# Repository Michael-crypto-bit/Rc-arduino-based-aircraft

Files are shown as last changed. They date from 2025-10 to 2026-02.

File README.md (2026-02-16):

a repository of all files needed to recreate my aircraft, only use the most updated ones as some originals were dicarded, and are only here to show the path I took
items needed:
2 ESCs 30-40a with 2200kv motors                                                                                                                                                    
arduino Nano
2 micro servos
xt-60 cable y splitter male to dual female output                                                                                                                                                                
plastic glue                                                                                                 
duct tape                                                                                                                                                                                            
foam                                                                                                      
fpv camera optional                                                                                                                                                                                           
fishing wire optional                                                                                                                   
wooden dowels                                                                                                                                                        
lipo battery - must match the draw of motors, they will power arduino in turn                                                                                                   
lw pla and 3d printer                                                                                                                                                                               
a lasercutter with lightweight wood medium basswood hardwood or balsa
assembly steps: 
1) 3d print wings with lw pla and attach to each other with wooden dowels, the dowels will slot into the small circular holes in the side of each wing segment
2) screw in 2200kv motors and connect ESC's sliding the ESC into the larger hole in the wing, once for each wing
3) put in servos into the smaller hole with the arm base facing towards the trailing edge of the wing, with cable exstensions going in the direction of the 2200 kv motors and eventually towards the body. All cables will run through the holes in the wing


5) after all electronics are placed and dowels have been slotted into the wings enclose with duck tape to bind the wings together and enclose electronics
6) assemble the body sections with glue, attach rear wings with two more dowels or thick wire and glue in place
7) carve a the rear tail out of foam and attach with dowels and glue

8) slot the wings onto the front of the body and route wires through the roof of the electronics compartment, attach optional camera through the front mounting hole
9) if the wings are too heavy for the dowels, and they start to bend use fishing wire and wooden support on the roof in a tent style to raise the wings, or use dowels underneath the wing
    
11) insert the bread board, arduino nano, and switch into the electronics compartment, making sure the switch is secure and electronically sound
    
12) when ready to fly program the arduino and plug in the lipo battery into a cable splitter connecting the two ESC's and the plane will start on its own
                                                                                                          
link to documentation: https://docs.google.com/document/d/1xMwoFOoDOEly96luMzOv4UvHKFmw87LAqAQyq4E37es/edit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                                                              
-------------------------------------------------------UPDATE 1/5/2026--------------------------------------------------
I have designed an all in one pcb board for the arduino pro mini and extras including a reciever, gyro and more all in one board. I am moving to the arduino pro mini mainly for it's size while still having the same arduino base which is the purpose of this project. These are being shipped from pcbway.com and the review will be uploaded shortly.
    This update will allow the aircraft to be fully rc, arduino code is soon to follow.
-------------------------------------------------------UPDATE 2/4/2026--------------------------------------------------
The long awaited pcb boards have arrived from PCBway.com. At a firts glance they look quite professional in their black, their is no issues or malformations in their design. I am very happy with the quality. Pictures are soon to follow. My complete review will be updated when I have completely sautered and tested the pcb boards.
-------------------------------------------------------UPDATE 2/16/2026---------------------------------------------------                                                                                           
Assembly has started for the PCB boards, and v1 of the gerbers will be uploaded to this repository, also here are the pictures that were promised, again a great thanks to PCBway.com for generously supplying these high quality PCB boards. The files for the transmitter can be found on https://howtomechatronics.com/projects/diy-arduino-rc-transmitter/







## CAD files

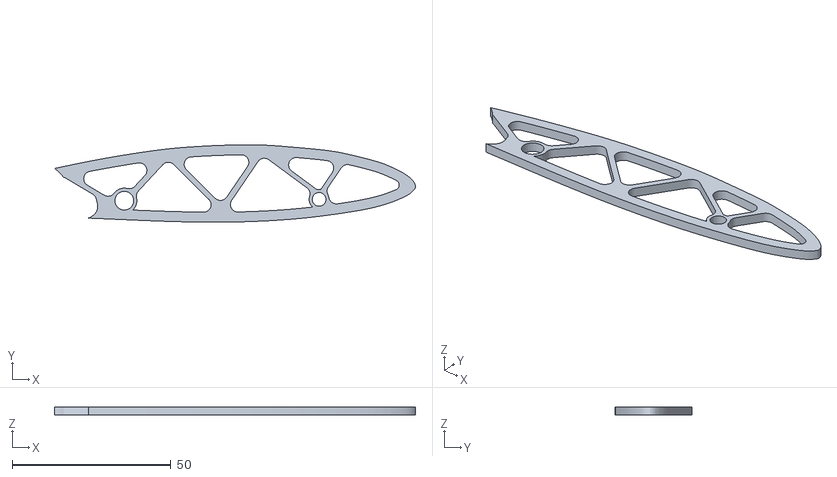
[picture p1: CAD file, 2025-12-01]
Airfoil v7 struts.stl
113.8 x 24.4 x 2.54

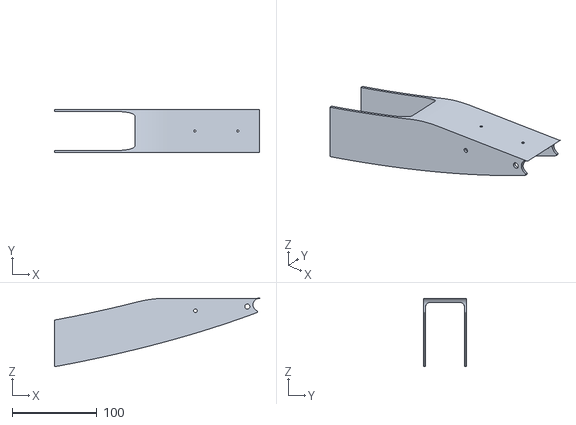
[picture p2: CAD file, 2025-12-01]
plane v1 with 7 inch wings rear.stl
241.5 x 50.8 x 80.7

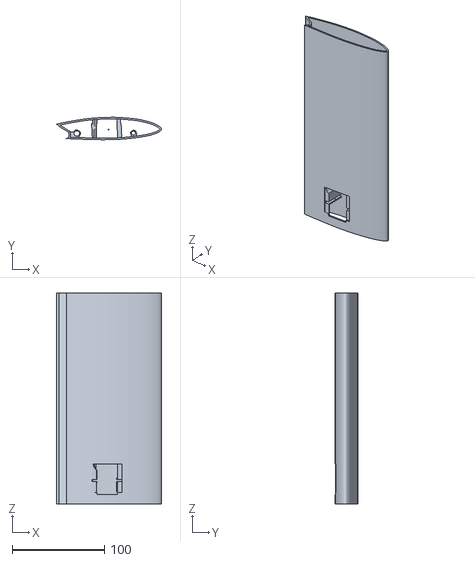
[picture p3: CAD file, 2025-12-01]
Airfoil v7 lightweight single.stl
113.8 x 24.4 x 228.6

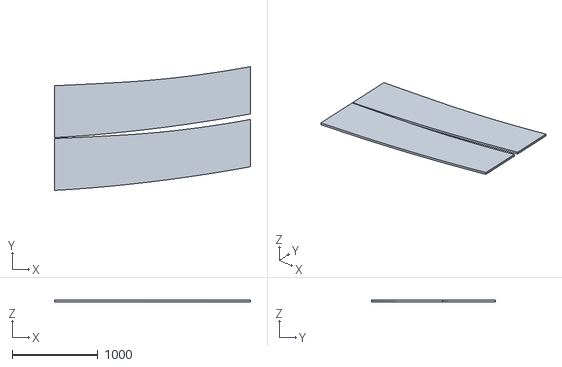
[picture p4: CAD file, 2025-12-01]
plane v2 with 7 inch wings side panel.stl
2280.4 x 1440.6 x 26.0

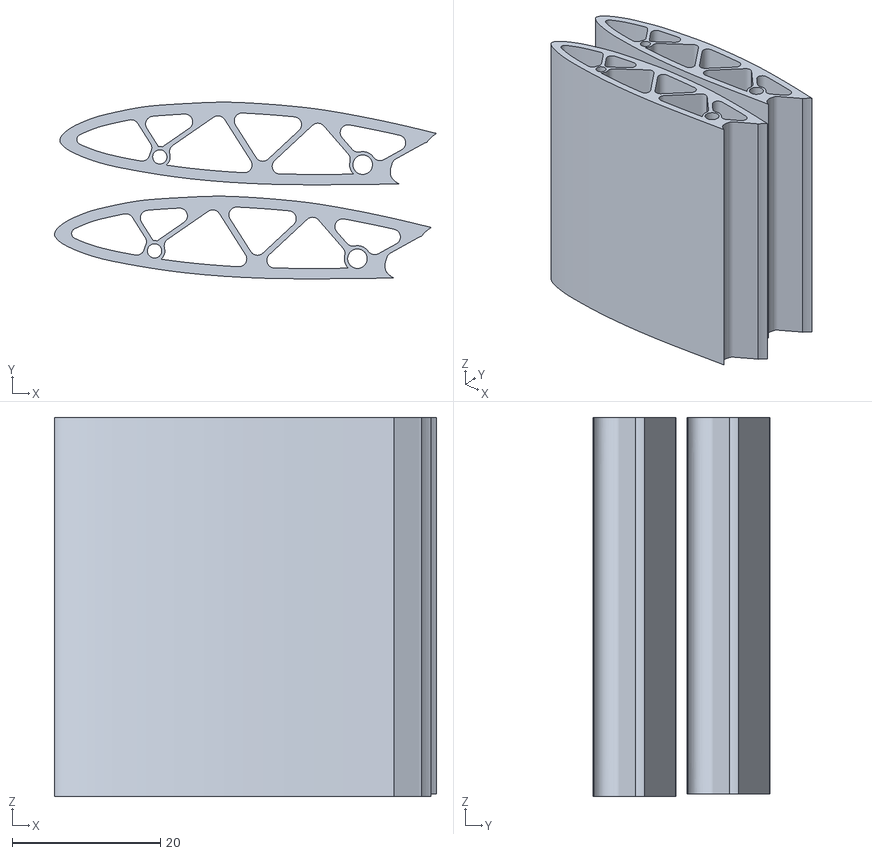
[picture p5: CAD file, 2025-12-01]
rear wings.stl
51.5 x 23.8 x 51.2

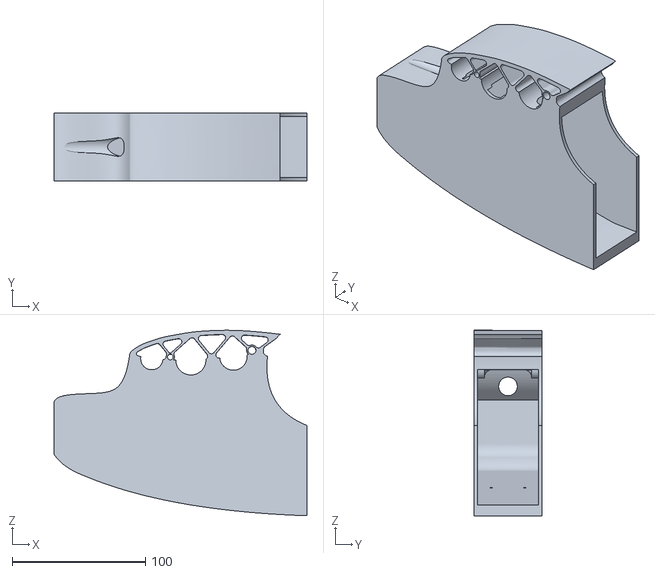
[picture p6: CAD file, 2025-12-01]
v3 front of plane.stl
189.7 x 50.8 x 139.1

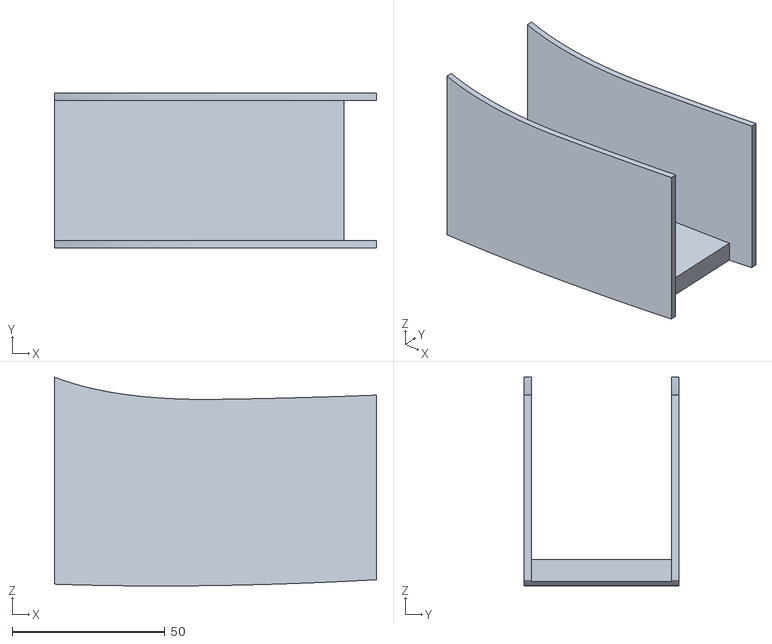
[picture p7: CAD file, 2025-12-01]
front middle section.stl
105.3 x 50.8 x 68.3

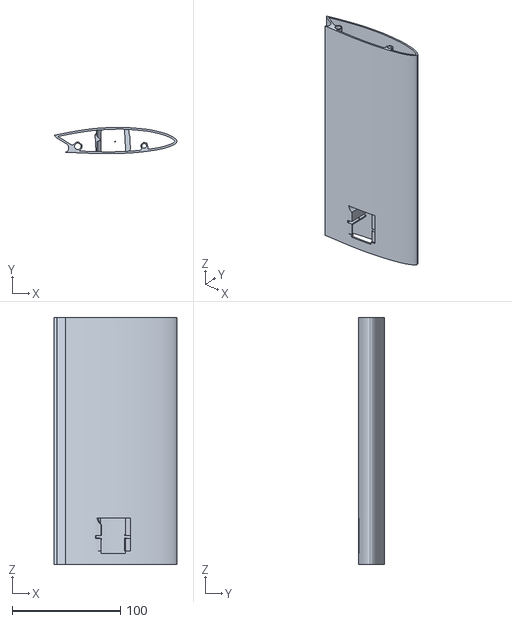
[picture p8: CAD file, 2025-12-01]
Airfoil v6 single lightweight.stl
113.8 x 24.4 x 228.6

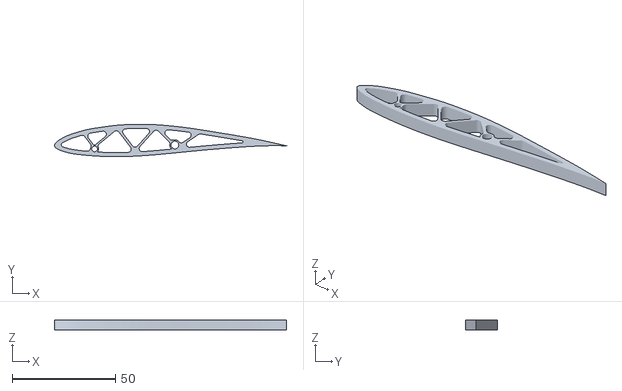
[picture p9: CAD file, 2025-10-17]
Airfoil.stl
112.4 x 15.6 x 5.00

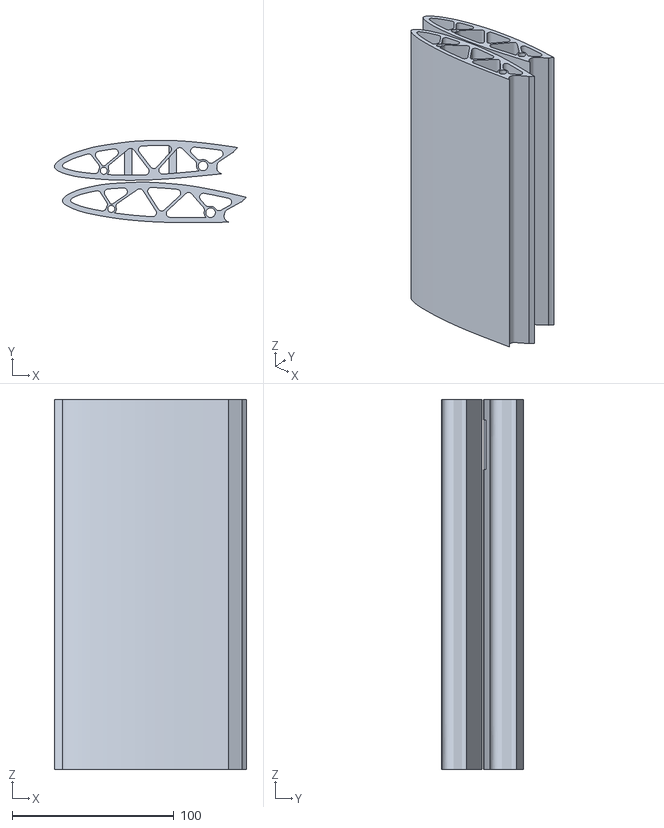
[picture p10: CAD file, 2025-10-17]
Airfoil v5.stl
118.8 x 50.7 x 228.6

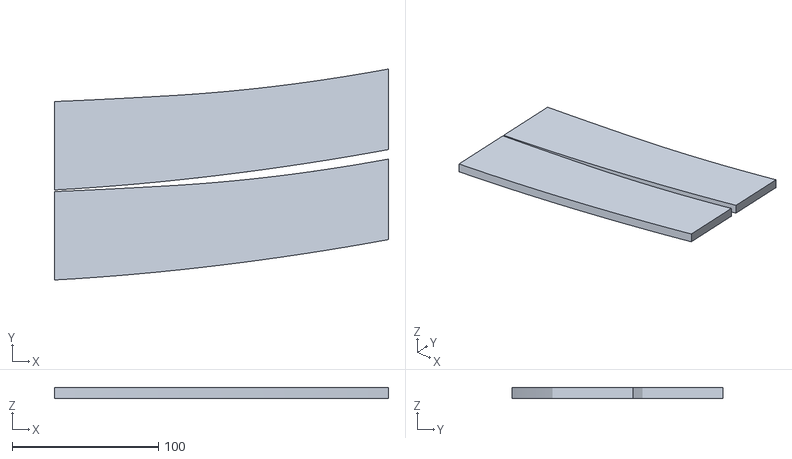
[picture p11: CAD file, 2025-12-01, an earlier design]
plane v1 with 7 inch wings side panel.stl
228.0 x 144.1 x 7.79

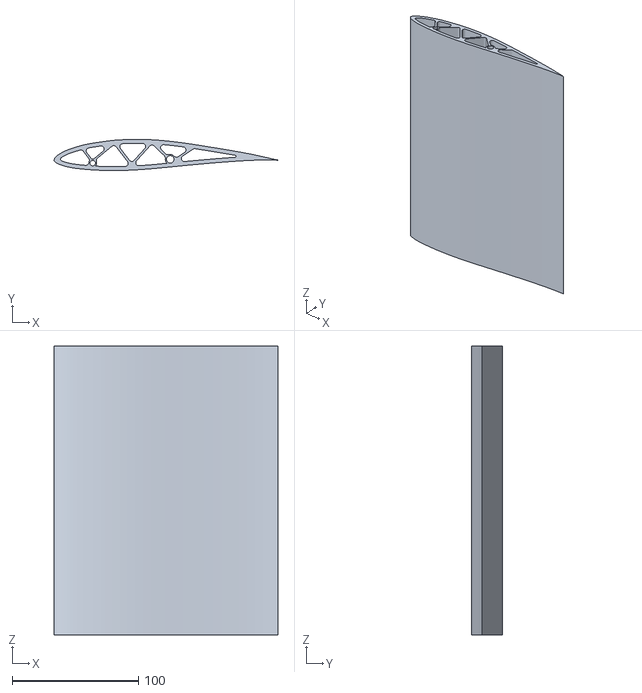
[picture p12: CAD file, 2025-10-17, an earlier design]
Airfoil v3.stl
177.0 x 24.6 x 228.6

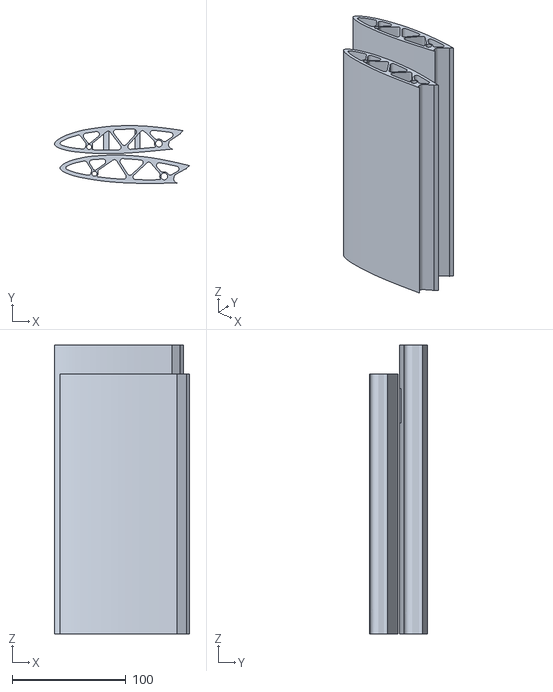
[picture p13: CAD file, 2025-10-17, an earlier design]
Airfoil v4.stl
118.8 x 50.7 x 254.0

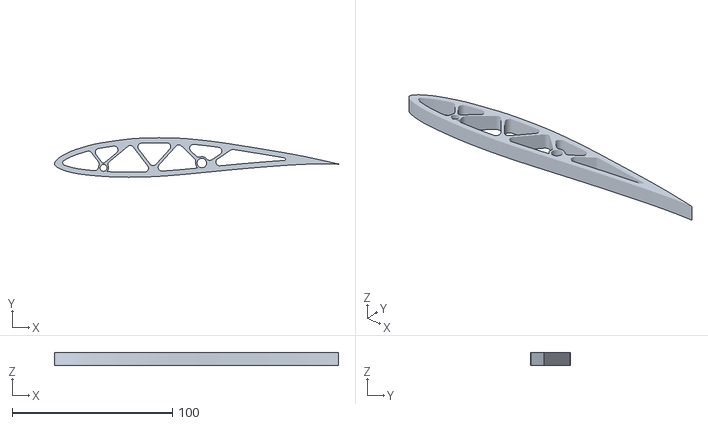
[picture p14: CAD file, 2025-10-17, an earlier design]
Airfoil v1.stl
177.0 x 24.6 x 7.87

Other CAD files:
Airfoil v2.stl

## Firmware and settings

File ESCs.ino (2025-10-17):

#include <Servo.h>
#define CLK 11
#define DT 10

int counter = 20;
int currentStateCLK;
int lastStateCLK;
String currentDir = "";

Servo ESB;
Servo ESC; 

int Speed; 

void setup(){
  Serial.begin(9600);
ESB.attach(12,1000,2000);
ESC.attach(9,1000,2000);
  pinMode(CLK, INPUT);
  pinMode(DT, INPUT);
  lastStateCLK = digitalRead(CLK);
}

void loop(){

  // Read the current state of CLK
  currentStateCLK = digitalRead(CLK);

  // If last and current state of CLK are different, then pulse occurred
  // React to only 1 state change to avoid double count
  if (currentStateCLK != lastStateCLK && currentStateCLK == 1) {

    // If the DT state is different than the CLK state then
    // the encoder is rotating CCW so decrement
    if (digitalRead(DT) != currentStateCLK) {
      counter--;
      currentDir = "CCW";
    } else {
      // Encoder is rotating CW so increment
      counter++;
      currentDir = "CW";
    }

    Serial.print(" | Counter: ");
    Serial.println(counter);
  }

  // Remember last CLK state
  lastStateCLK = currentStateCLK;

  Speed = counter;
  ESB.write(Speed);
  ESC.write(Speed);
  delay(1);
}

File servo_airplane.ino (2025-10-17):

#include <Servo.h>
Servo leftwing;
Servo rightwing;
Servo backLeft;
Servo backRight;
int pos = 0;
const int SW_pin = 7;
const int X_pin = 2;
const int Y_pin = 3;
const int SW2_pin = 10; 
const int X2_pin = 0; 
const int Y2_pin = 1; 

void setup() {
  leftwing.attach(9);
  rightwing.attach(8);
   backLeft.attach(5);
    backRight.attach(6);
  pinMode(SW_pin, INPUT);
  digitalWrite(SW_pin, HIGH);
    pinMode(SW2_pin, INPUT);
  digitalWrite(SW2_pin, HIGH);
  Serial.begin(9600);
  leftwing.write(0);
  rightwing.write(0);
  backLeft.write(0);
  backRight.write(0);
}

void loop() {
  Serial.print("Switch:  ");
  Serial.print(digitalRead(SW_pin));
  Serial.print(" | ");
  Serial.print("X-axis: ");
  Serial.print(analogRead(X2_pin));
  Serial.print(" | ");
  Serial.print("Y-axis: ");
  Serial.print(analogRead(Y2_pin));
  Serial.println(" | ");
  delay(200);
  if(analogRead(Y2_pin)>=520){
leftwing.write(45);
rightwing.write(45);
backLeft.write(45);
backRight.write(45);
  }
  else if(analogRead(Y2_pin)<=500){
leftwing.write(135);
rightwing.write(135);
backLeft.write(135);
backRight.write(135);
  }
  else if(analogRead(X_pin)>=700){
leftwing.write(160);
rightwing.write(20);
  }
    else if(analogRead(X_pin)>=525){
leftwing.write(135);
rightwing.write(45);                
  }
  else if(analogRead(X_pin)<=254){
leftwing.write(20); 
rightwing.write(160);                    
  }
    else if(analogRead(X_pin)<=514){
leftwing.write(45);   
rightwing.write(135);                  
  }
 else{
  leftwing.write(90);
  rightwing.write(90);
 }
  }
